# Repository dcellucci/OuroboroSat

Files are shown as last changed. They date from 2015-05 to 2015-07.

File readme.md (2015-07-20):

#The Ouroboros Modular Satellite

 > I was sitting, writing at my text-book; but the work did not progress; my thoughts were elsewhere. I turned my chair to the fire and dozed. Again the atoms were gamboling before my eyes. This time the smaller groups kept modestly in the background. My mental eye, rendered more acute by the repeated visions of the kind, could now distinguish larger structures of manifold conformation: long rows, sometimes more closely fitted together; all twining and twisting in snake-like motion. But look! What was that? One of the snakes had seized hold of its own tail, and the form whirled mockingly before my eyes. As if by a flash of lightning I awoke; and this time also I spent the rest of the night in working out the consequences of the hypothesis.
 > ([August Kekulé](https://en.wikipedia.org/wiki/Ouroboros#Chemistry))

Ouroboros is the modular satellite platform that combines communication, power-sharing, and the Arduino framework to create a scalable platform for orbital experiments. It's designed to be even smaller than a CubeSat (one sixth, to be exact)

##What does it do?

The Ouroboros board (v. 1.0) can do alot of things. 

  1. It behaves like an Arduino, so it can run Arduino code and libraries
  2. It has the ability to charge an on-board LiPo battery from a solar panel
  3. It can connect to a maximum of four neighbors, and can talk to these four neighbors using a protocol called the Asynchronous Packet Automaton (which you can learn more about [here](https://github.com/dcellucci/APA_Tutorial)).
  4. It can also use this connection to charge a neighbor's battery using its own on-board battery, for which there are plenty of reasons, detailed in a forthcoming paper. 

Ouroboros is supposed to be alot like the Iron Man suit- it's the foundation upon which a more complex and specialized iterations can be built. My goal is to make the process of extending both the hardware and the software as easy and transparent as possible.

##Installation

You'll first want to install the software libraries- Ouroboros and its dependencies- as well as the hardware board specification. 

 * To install the software libraries, simply copy the contents of `code/libraries` folder to the `libraries` directory of your Arduino sketchbook (you might have to make it). 
 * To install the board spec, copy the contents of `code/hardware` to the `hardware` directory of the sketchbook (you might thave to make that directory as well).

Check out the [advanced installation guide](code/install.md) for a method that doesn't require copying using symbolic links (Linux/OSX only).

##Getting Started
There are plenty of ways to get started. Probably the first and best way is to make your own prototype on a breadboard, which is detailed inside the `boards/breadboard` folder. That way you can practice with the wiring and the code, as well as test what you'll need to add to the existing Ouroboros board in order to get it working with your project.

The `Blank_Example` sketch provides a bare-bones implementation of the Ouroboros functionality-

##License

<br />This work is licensed under a <a rel="license" href="http://creativecommons.org/licenses/by-sa/4.0/">Creative Commons Attribution-ShareAlike 4.0 International License</a>.

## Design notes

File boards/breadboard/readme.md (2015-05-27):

##Breadboard Ouroboros

Ouroboros can be assembled on a breadboard to quickly test whether it works with your project without having to order the finished board. 

The breadboard prototype consists of:

 * Arduino Pro Mini (3.3 V, 8 Mhz, ATMega 328P)
 * LiPo Battery (> 800 mAh capacity)
 * LiPo Fuel Gauge (MAX17043)
 * MPPT Solar Charger (LT3652)
 * P-Channel MOSFET (NDP-6020P)
 * Step-Up Converter (Pololu U3V12F9)

Almost all of the parts are available from Sparkfun ([wishlist](https://www.sparkfun.com/wish_lists/112185)) for less than $100 (USD), including the breadboard and jumper wires. The only piece missing is the DC-DC boost converter, which can be purchased from [Pololu](https://www.pololu.com/product/2116).

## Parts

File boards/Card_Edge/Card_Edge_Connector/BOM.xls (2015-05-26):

Item # | Qty | Ref Des | Manufacturer | Mfg Part # | Dist. Part # | Description | Package | Type
1 | 2 | U$1, U$2 | 3M | SPD08-020-LRB-TR | 517-SPD08-020-LRB-TR | Standard Card Edge Connectors SPD08, 20P, w/ Latch .76umAU | Custom | smt
 |  |  |  |  |  | BOARD SUMMARY FOR QUOTE
 |  |  |  |  |  | Total # of unique parts | 1
 |  |  |  |  |  | SMT placements per board | 2
 |  |  |  |  |  | Thru-hole placements per board | 0
 |  |  |  |  |  | Fine pitch placements per board | 0
 |  |  |  |  |  | BGA placements per board | 0

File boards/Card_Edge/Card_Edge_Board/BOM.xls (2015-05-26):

Item # | Qty | Ref Des | Manufacturer | Mfg Part # | Dist. Part # | Description | Package | Type
1 | 3 | C3,C4,C5 | Kemet | C1206C104K5RAC7867 | 399-1249-1-ND | CAP CER 0.1UF 50V 10% X7R 1206 | 1206 | smt
2 | 1 | R7 | Panasonic | ERJ-8RQFR22V | P.22RCT-ND | RES 0.22 OHM 1/4W 1% 1206 SMD | 1206 | smt
3 | 3 | C13,C15,C17 | Kemet | C1206C105K3RACTU | 399-1255-1-ND | CAP CER 1UF 25V 10% X7R 1206 | 1206 | smt
4 | 4 | C1,C2,C11,C14 | Taiyo Yuden | TMK316F106ZL-T | 587-1353-1-ND | CAP CER 10UF 25V Y5V 1206 | 1206 | smt
5 | 1 | R2 | Panasonic | ERJ-8ENF1003V | P100KFCT-ND | RES 100K OHM 1/4W 1% 1206 SMD | 1206 | smt
6 | 7 | R1, R8, R9, R10,R11,R12,R13 | Panasonic | ERJ-8GEYJ103V | P10KECT-ND | RES 10K OHM 1/4W 5% 1206 SMD | 1206 | smt
7 | 1 | C16 | Kemet | C1206C103K5RACTU | 399-1234-1-ND | CAP CER 10000PF 50V 10% X7R 1206 | 1206 | smt
8 | 1 | R18 | Panasonic | ERJ-8GEYJ102V | P1.0KECT-ND | RES 1K OHM 1/4W 5% 1206 SMD | 1206 | smt
9 | 2 | C6,C9 | Kemet | C1206C200K5GACTU | 399-9326-1-ND | CAP CER 20PF 50V 10% NP0 1206 | 1206 | smt
10 | 1 | R4 | Panasonic | ERJ-8GEYJ304V | P300KECT-ND | RES 300K OHM 1/4W 5% 1206 SMD | 1206 | smt
11 | 4 | R3,R5,R6,R14 | Panasonic | ERJ-8GEYJ472V | P4.7KECT-ND | RES 4.7K OHM 1/4W 5% 1206 SMD | 1206 | smt
12 | 2 | C7,C8 | Rohm Semiconductor | TCTAL1A476M8R | 511-1500-1-ND | CAP TANT 47UF 10V 20% 1206 | 1206 | smt
13 | 1 | L5 | Bourns Fixed Inductors | SRN6028-680M | SRN6028-680MCT-ND | INDUCTOR POWER 68UH SMD | see DS | smt
14 | 1 | U1 | Atmel | ATMEGA328P-AUR | ATMEGA328P-AURCT-ND | IC MCU 8BIT 32KB FLASH | 32TQFP | fine pitch
15 | 1 | y1 | Murata | CSTCE8M00G55Z-R0 | 490-1219-1-ND | CER RESONATOR 8.00MHZ SMD | 3-SMD, Non-Standard | smt
16 | 1 | Q1 | Fairchild | FDN360P | FDN360PCT-ND | MOSFET P-CH 30V 2A SSOT3 | SSOP-3 | smt
17 | 1 | U3 | Linear Technology | LT3652EMSE#PBF | 64R8539 | IC, BATTERY CHARGER, 2A, | MSOP-12 | fine pitch
18 | 1 | U4 | Maxim Integrated | MAX17043G+U | 700-MAX17043G+U | LiPo Fuel Gauge | TDFN-8 | smt | http://www.maximintegrated.com/en/products/power/battery-management/MAX17043.html/tb_tab3
19 | 1 | U2 | Micrel | MIC5205-3.3YM5 TR | 576-1259-1-ND | IC REG LDO 3.3V 0.15A SOT23-5 | SOT23-5 | smt
20 | 9 | D1,D6,D7,D8,D9,D10,D11,D12,D13 | Diodes Inc | SBR130S3-7 | SBR130S3-7DICT-ND | DIODE SUPR BARRIER 30V 1A | SOD323 | smt
21 | 4 | D2,D3,D4,D5 | Diodes Inc | ZLLS500TA | 522-ZLLS500TA | Schottky Diodes & Rectifiers 500mA Low Leak Sch | SOT-23 | smt
 |  |  |  |  |  | BOARD SUMMARY FOR QUOTE
 |  |  |  |  |  | Total # of unique parts | 21
 |  |  |  |  |  | SMT placements per board | 48
 |  |  |  |  |  | Thru-hole placements per board | 0
 |  |  |  |  |  | Fine pitch placements per board | 2
 |  |  |  |  |  | BGA placements per board | 0

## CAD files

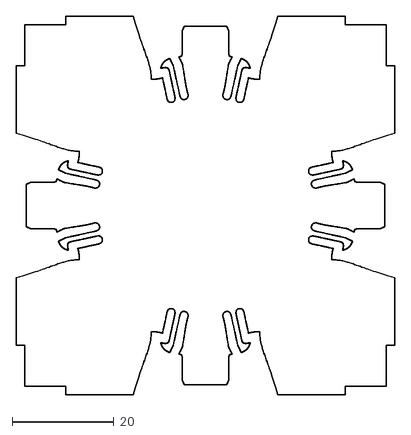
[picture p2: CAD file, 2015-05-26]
boards/Card_Edge/Card_Edge_Board/snap_connector_rev_2.dxf
74.6 x 74.6

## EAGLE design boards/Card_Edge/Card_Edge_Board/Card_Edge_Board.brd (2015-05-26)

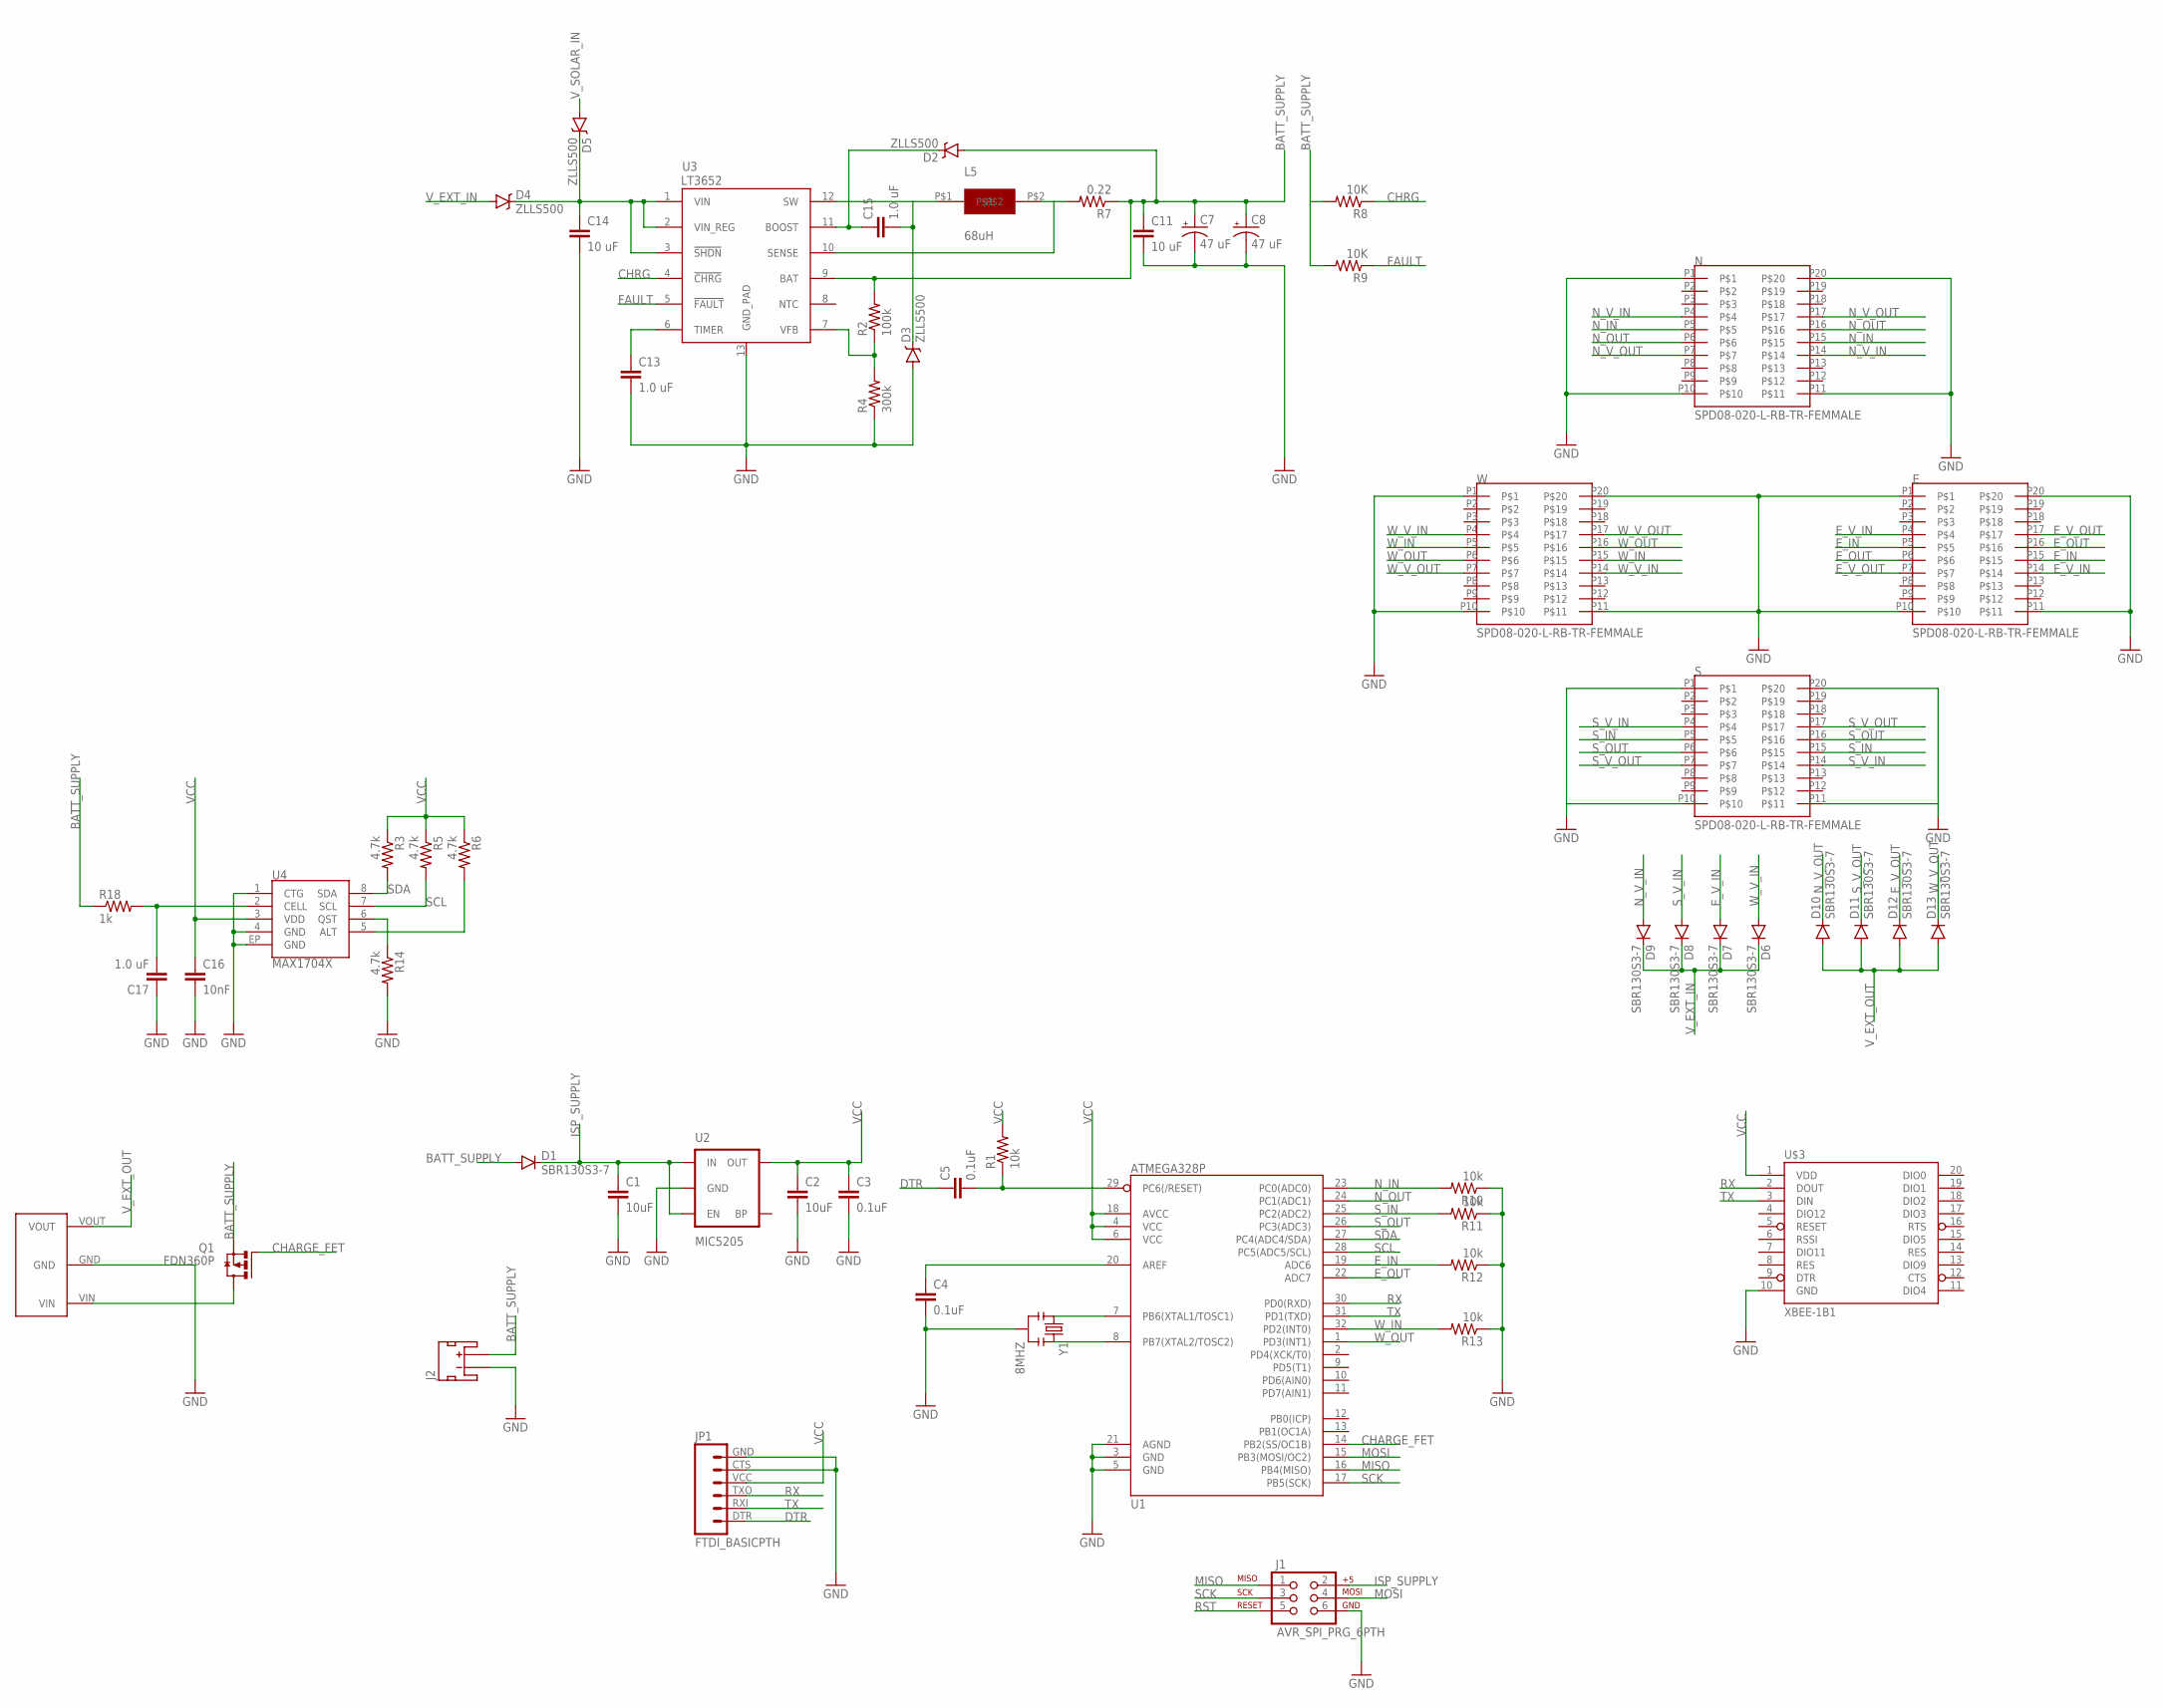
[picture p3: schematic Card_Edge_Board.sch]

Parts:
C1, C2: 10uF; 1206
C3, C4, C5: 0.1uF; 1206
C7, C8: 47 uF; EIA3216
C11, C14: 10 uF; 1206
C13, C15, C17: 1.0 uF; 1206
C16: 10nF; 1206
D1, D6, D7, D8, D9, D10, D11, D12, D13: SBR130S3-7; SOD-323
D2, D3, D4, D5: ZLLS500; SOT23
E: SPD08-020-L-RB-TR-FEMMALE; SPD08-020-L-RB-TR-FOOT
J1: AVR_SPI_PRG_6PTH; 2X3
J2: JST_2MM_MALE; JST-2-SMD
JP1: FTDI_BASICPTH; FTDI_BASIC
L5: 68uH; MURATA_29L68C
N: SPD08-020-L-RB-TR-FEMMALE; SPD08-020-L-RB-TR-FOOT
Q1: FDN360P; SUPER-SOT3
R1, R10, R11, R12, R13: 10k; 1206
R2: 100k; 1206
R3, R5, R6, R14: 4.7k; 1206
R4: 300k; 1206
R7: 0.22; 1206
R8, R9: 10K; 1206
R18: 1k; 1206
S: SPD08-020-L-RB-TR-FEMMALE; SPD08-020-L-RB-TR-FOOT
U1: ATMEGA328P; TQFP32-08
U2: MIC5205; SOT23-5
U3: LT3652; MSOP-12_GND
U4: MAX1704X; TDFN-8
U$1: POLOLU791BOOSTPOLOLU; POLOLU791_BOOST
U$3: XBEE-1B1; XBEE-1
W: SPD08-020-L-RB-TR-FEMMALE; SPD08-020-L-RB-TR-FOOT
Y1: 8MHZ; RESONATOR-SMD

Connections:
BATT_SUPPLY: C7.A (+), C8.A (+), C11.1, D1.A, D2.1 (A), J2.2 (+), Q1.2 (S), R2.2, R7.1, R8.2, R9.2, R18.1, U3.9 (BAT)
CHARGE_FET: Q1.1 (G), U1.14 (PB2(SS/OC1B))
CHRG: R8.1, U3.4 (!CHRG)
DTR: C5.1, JP1.DTR (1)
E_IN: E.P5, E.P15, R12.2, U1.19 (ADC6)
E_OUT: E.P6, E.P16, U1.22 (ADC7)
E_V_IN: D7.A, E.P4, E.P14
E_V_OUT: D12.C, E.P7, E.P17
FAULT: R9.1, U3.5 (!FAULT)
GND: C1.2, C2.2, C3.2, C4.2, C7.C (-), C8.C (-), C11.2, C13.2, C14.2, C16.2, C17.1, D3.1 (A), E.P1, E.P10, E.P11, E.P20, J1.6, J2.1 (-), JP1.CTS (5), JP1.GND (6), N.P1, N.P10, N.P11, N.P20, R4.1, R10.1, R11.1, R12.1, R13.1, R14.2, S.P1, S.P10, S.P11, S.P20, U1.3 (GND), U1.5 (GND), U1.21 (AGND), U2.2 (GND), U3.13 (GND_PAD), U4.1 (CTG), U4.4 (GND), U4.EP (GND), U$1.GND, U$3.10 (GND), W.P1, W.P10, W.P11, W.P20, Y1.2
ISP_SUPPLY: C1.1, D1.C, J1.2, U2.1 (IN), U2.3 (EN)
MISO: J1.1, U1.16 (PB4(MISO))
MOSI: J1.4, U1.15 (PB3(MOSI/OC2))
unnamed: C13.1, U3.6 (TIMER)
unnamed: L5.P$2, R7.2, U3.10 (SENSE)
unnamed: C4.1, U1.20 (AREF)
unnamed: R6.2, U4.5 (ALT)
unnamed: R2.1, R4.2, U3.7 (VFB)
unnamed: C15.1, D2.3 (C), U3.11 (BOOST)
unnamed: C15.2, D3.3 (C), L5.P$1, U3.12 (SW)
unnamed: R14.1, U4.6 (QST)
unnamed: Q1.3 (D), U$1.VIN
unnamed: U1.8 (PB7(XTAL2/TOSC2)), Y1.3
unnamed: U1.7 (PB6(XTAL1/TOSC1)), Y1.1
unnamed: C17.2, R18.2, U4.2 (CELL)
unnamed: C14.1, D4.3 (C), D5.3 (C), U3.1 (VIN), U3.2 (VIN_REG), U3.3 (!SHDN)
N_IN: N.P5, N.P15, R10.2, U1.23 (PC0(ADC0))
N_OUT: N.P6, N.P16, U1.24 (PC1(ADC1))
N_V_IN: D9.A, N.P4, N.P14
N_V_OUT: D10.C, N.P7, N.P17
RST: C5.2, J1.5, R1.1, U1.29 (PC6(/RESET))
RX: JP1.TXO (3), U1.30 (PD0(RXD)), U$3.2 (DOUT)
SCK: J1.3, U1.17 (PB5(SCK))
SCL: R5.2, U1.28 (PC5(ADC5/SCL)), U4.7 (SCL)
SDA: R3.2, U1.27 (PC4(ADC4/SDA)), U4.8 (SDA)
S_IN: R11.2, S.P5, S.P15, U1.25 (PC2(ADC2))
S_OUT: S.P6, S.P16, U1.26 (PC3(ADC3))
S_V_IN: D8.A, S.P4, S.P14
S_V_OUT: D11.C, S.P7, S.P17
TX: JP1.RXI (2), U1.31 (PD1(TXD)), U$3.3 (DIN)
VCC: C2.1, C3.1, C16.1, JP1.VCC (4), R1.2, R3.1, R5.1, R6.1, U1.4 (VCC), U1.6 (VCC), U1.18 (AVCC), U2.5 (OUT), U4.3 (VDD), U$3.1 (VDD)
V_EXT_IN: D4.1 (A), D6.C, D7.C, D8.C, D9.C
V_EXT_OUT: D10.A, D11.A, D12.A, D13.A, U$1.VOUT
V_SOLAR_IN: D5.1 (A)
W_IN: R13.2, U1.32 (PD2(INT0)), W.P5, W.P15
W_OUT: U1.1 (PD3(INT1)), W.P6, W.P16
W_V_IN: D6.A, W.P4, W.P14
W_V_OUT: D13.C, W.P7, W.P17

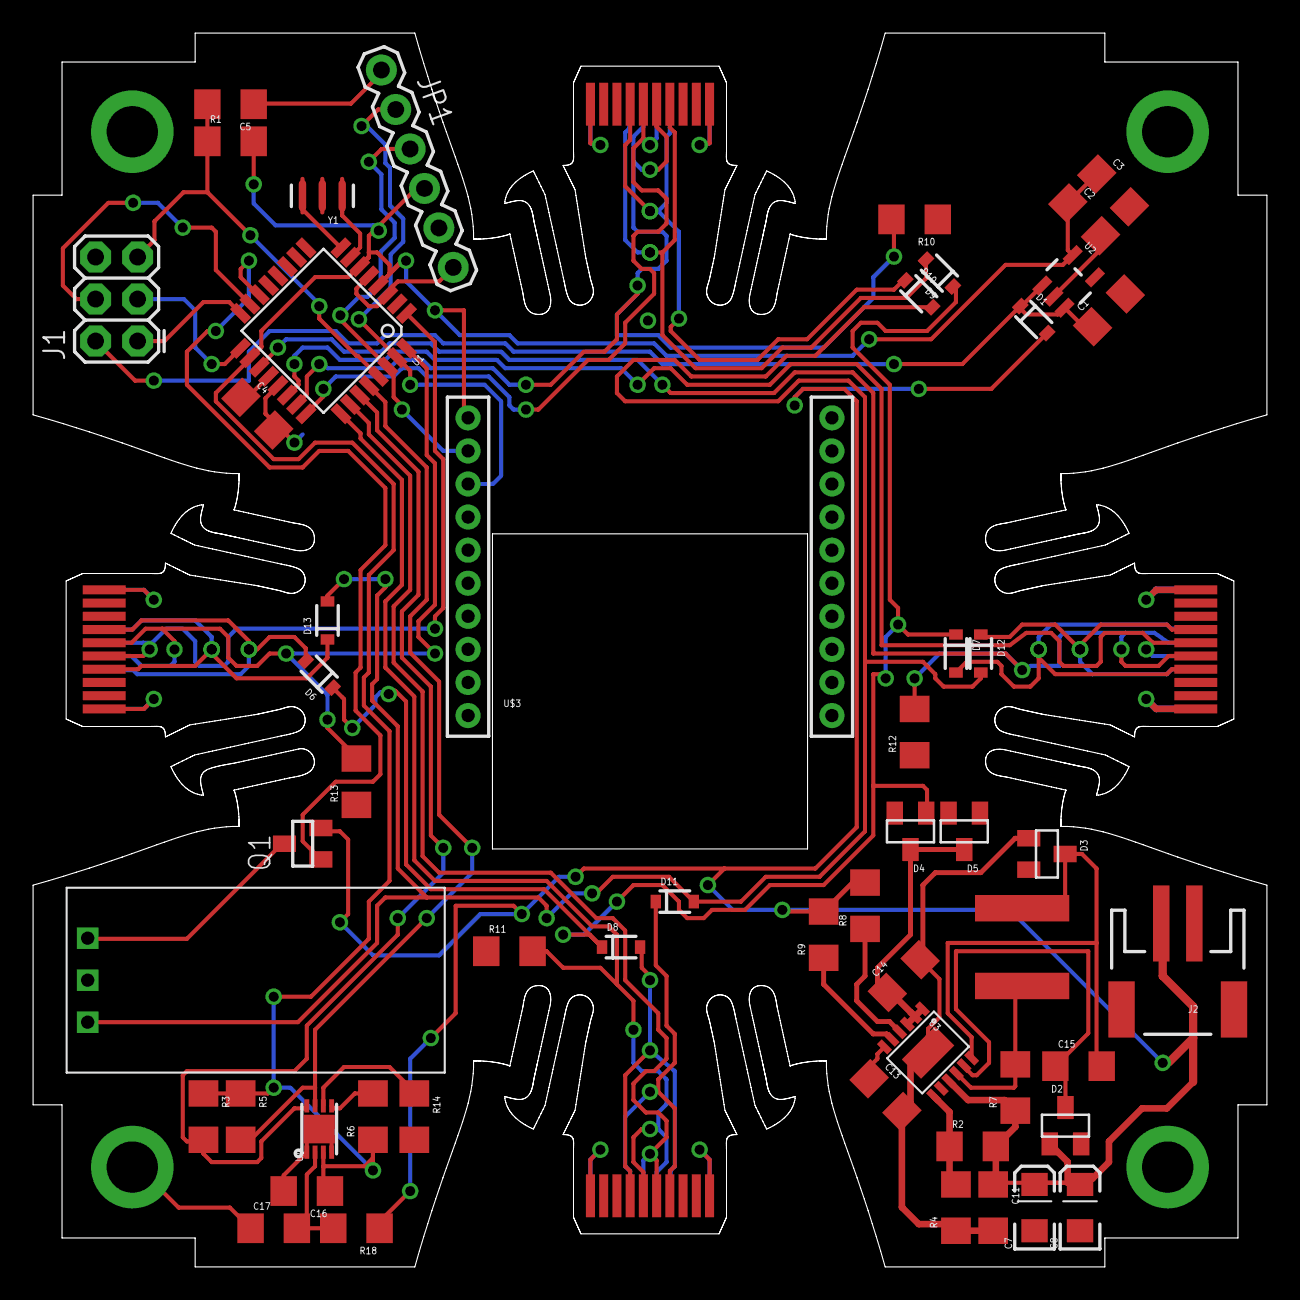
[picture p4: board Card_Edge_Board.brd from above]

Board: 2 copper layers, 74.6 x 74.6 mm, 57 parts (0 on the bottom side), 47 nets.

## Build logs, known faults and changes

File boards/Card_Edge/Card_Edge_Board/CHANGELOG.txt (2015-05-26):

Things to change

1) Use something other than ADC6/ADC7 as the APA east channel.

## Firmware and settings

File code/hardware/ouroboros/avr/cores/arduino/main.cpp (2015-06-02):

/*
  main.cpp - Main loop for Arduino sketches
  Copyright (c) 2005-2013 Arduino Team.  All right reserved.

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
  You should have received a copy of the GNU Lesser General Public
  License along with this library; if not, write to the Free Software
  Foundation, Inc., 51 Franklin St, Fifth Floor, Boston, MA  02110-1301  USA
*/

#include <Arduino.h>
//Declared weak in Arduino.h to allow user redefinitions.
int atexit(void (*func)()) { return 0; }
// Weak empty variant initialization function.
// May be redefined by variant files.
void initVariant() __attribute__((weak));

void initVariant() { 
//Serial.begin(9600);
}

int main(void)
{
	init();

	initVariant();

#if defined(USBCON)
	USBDevice.attach();
#endif
	
	setup();
    
	for (;;) {
    //Board.heartbeat();
		loop();
		if (serialEventRun) serialEventRun();
	}
        
	return 0;
}

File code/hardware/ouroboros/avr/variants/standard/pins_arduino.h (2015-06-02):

/*
  pins_arduino.h - Pin definition functions for Arduino
  Part of Arduino - http://www.arduino.cc/

  Copyright (c) 2007 David A. Mellis

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
  $Id: wiring.h 249 2007-02-03 16:52:51Z mellis $
*/

#ifndef Pins_Arduino_h
#define Pins_Arduino_h

#include <avr/pgmspace.h>

#define NUM_DIGITAL_PINS            20
#define NUM_ANALOG_INPUTS           6
#define analogInputToDigitalPin(p)  ((p < 6) ? (p) + 14 : -1)

#if defined(__AVR_ATmega8__)
#define digitalPinHasPWM(p)         ((p) == 9 || (p) == 10 || (p) == 11)
#else
#define digitalPinHasPWM(p)         ((p) == 3 || (p) == 5 || (p) == 6 || (p) == 9 || (p) == 10 || (p) == 11)
#endif

static const uint8_t SS   = 10;
static const uint8_t MOSI = 11;
static const uint8_t MISO = 12;
static const uint8_t SCK  = 13;

static const uint8_t SDA = 18;
static const uint8_t SCL = 19;
#define LED_BUILTIN 13

static const uint8_t A0 = 14;
static const uint8_t A1 = 15;
static const uint8_t A2 = 16;
static const uint8_t A3 = 17;
static const uint8_t A4 = 18;
static const uint8_t A5 = 19;
static const uint8_t A6 = 20;
static const uint8_t A7 = 21;

#define digitalPinToPCICR(p)    (((p) >= 0 && (p) <= 21) ? (&PCICR) : ((uint8_t *)0))
#define digitalPinToPCICRbit(p) (((p) <= 7) ? 2 : (((p) <= 13) ? 0 : 1))
#define digitalPinToPCMSK(p)    (((p) <= 7) ? (&PCMSK2) : (((p) <= 13) ? (&PCMSK0) : (((p) <= 21) ? (&PCMSK1) : ((uint8_t *)0))))
#define digitalPinToPCMSKbit(p) (((p) <= 7) ? (p) : (((p) <= 13) ? ((p) - 8) : ((p) - 14)))

#define digitalPinToInterrupt(p)  ((p) == 2 ? 0 : ((p) == 3 ? 1 : NOT_AN_INTERRUPT))

#ifdef ARDUINO_MAIN

// On the Arduino board, digital pins are also used
// for the analog output (software PWM).  Analog input
// pins are a separate set.

// ATMEL ATMEGA8 & 168 / ARDUINO
//
//                  +-\/-+
//            PC6  1|    |28  PC5 (AI 5)
//      (D 0) PD0  2|    |27  PC4 (AI 4)
//      (D 1) PD1  3|    |26  PC3 (AI 3)
//      (D 2) PD2  4|    |25  PC2 (AI 2)
// PWM+ (D 3) PD3  5|    |24  PC1 (AI 1)
//      (D 4) PD4  6|    |23  PC0 (AI 0)
//            VCC  7|    |22  GND
//            GND  8|    |21  AREF
//            PB6  9|    |20  AVCC
//            PB7 10|    |19  PB5 (D 13)
// PWM+ (D 5) PD5 11|    |18  PB4 (D 12)
// PWM+ (D 6) PD6 12|    |17  PB3 (D 11) PWM
//      (D 7) PD7 13|    |16  PB2 (D 10) PWM
//      (D 8) PB0 14|    |15  PB1 (D 9) PWM
//                  +----+
//
// (PWM+ indicates the additional PWM pins on the ATmega168.)

// ATMEL ATMEGA1280 / ARDUINO
//
// 0-7 PE0-PE7   works
// 8-13 PB0-PB5  works
// 14-21 PA0-PA7 works 
// 22-29 PH0-PH7 works
// 30-35 PG5-PG0 works
// 36-43 PC7-PC0 works
// 44-51 PJ7-PJ0 works
// 52-59 PL7-PL0 works
// 60-67 PD7-PD0 works
// A0-A7 PF0-PF7
// A8-A15 PK0-PK7


// these arrays map port names (e.g. port B) to the
// appropriate addresses for various functions (e.g. reading
// and writing)
const uint16_t PROGMEM port_to_mode_PGM[] = {
	NOT_A_PORT,
	NOT_A_PORT,
	(uint16_t) &DDRB,
	(uint16_t) &DDRC,
	(uint16_t) &DDRD,
};

const uint16_t PROGMEM port_to_output_PGM[] = {
	NOT_A_PORT,
	NOT_A_PORT,
	(uint16_t) &PORTB,
	(uint16_t) &PORTC,
	(uint16_t) &PORTD,
};

const uint16_t PROGMEM port_to_input_PGM[] = {
	NOT_A_PORT,
	NOT_A_PORT,
	(uint16_t) &PINB,
	(uint16_t) &PINC,
	(uint16_t) &PIND,
};

const uint8_t PROGMEM digital_pin_to_port_PGM[] = {
	PD, /* 0 */
	PD,
	PD,
	PD,
	PD,
	PD,
	PD,
	PD,
	PB, /* 8 */
	PB,
	PB,
	PB,
	PB,
	PB,
	PC, /* 14 */
	PC,
	PC,
	PC,
	PC,
	PC,
};

const uint8_t PROGMEM digital_pin_to_bit_mask_PGM[] = {
	_BV(0), /* 0, port D */
	_BV(1),
	_BV(2),
	_BV(3),
	_BV(4),
	_BV(5),
	_BV(6),
	_BV(7),
	_BV(0), /* 8, port B */
	_BV(1),
	_BV(2),
	_BV(3),
	_BV(4),
	_BV(5),
	_BV(0), /* 14, port C */
	_BV(1),
	_BV(2),
	_BV(3),
	_BV(4),
	_BV(5),
};

const uint8_t PROGMEM digital_pin_to_timer_PGM[] = {
	NOT_ON_TIMER, /* 0 - port D */
	NOT_ON_TIMER,
	NOT_ON_TIMER,
	// on the ATmega168, digital pin 3 has hardware pwm
#if defined(__AVR_ATmega8__)
	NOT_ON_TIMER,
#else
	TIMER2B,
#endif
	NOT_ON_TIMER,
	// on the ATmega168, digital pins 5 and 6 have hardware pwm
#if defined(__AVR_ATmega8__)
	NOT_ON_TIMER,
	NOT_ON_TIMER,
#else
	TIMER0B,
	TIMER0A,
#endif
	NOT_ON_TIMER,
	NOT_ON_TIMER, /* 8 - port B */
	TIMER1A,
	TIMER1B,
#if defined(__AVR_ATmega8__)
	TIMER2,
#else
	TIMER2A,
#endif
	NOT_ON_TIMER,
	NOT_ON_TIMER,
	NOT_ON_TIMER,
	NOT_ON_TIMER, /* 14 - port C */
	NOT_ON_TIMER,
	NOT_ON_TIMER,
	NOT_ON_TIMER,
	NOT_ON_TIMER,
};

#endif
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

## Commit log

2015-01-27 The Ouroboros Satellite Board
    First Upload
2015-02-09 added lots of thing
    error checking functionality for lip fuel gauge
    and a blank sketch that shows how to make the barely functioning board
    work.
    [Ouroboros.cpp]
2015-05-26 Added the Card Edge Board
    [BOM.xls, Card_Edge_Board.brd, Card_Edge_Board.sch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]
2015-05-26 Added Card Edge Connector
    [BOM.xls, Card_Edge_Board.brd, Card_Edge_Board.sch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]
2015-05-27 Added breadboard
    Fritzing + Readme
    [breadboard.fzz]

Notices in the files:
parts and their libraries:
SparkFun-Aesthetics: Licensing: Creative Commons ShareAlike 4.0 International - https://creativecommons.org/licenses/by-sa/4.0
